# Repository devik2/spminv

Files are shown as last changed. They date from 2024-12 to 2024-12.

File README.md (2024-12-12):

# spminv

Simple IGBT motor inverter

Initial idea was independent but in 2024 when I started I borrowed
idea of heatsink from from STMBL project.

There are differences from STMBL, only one MCU located on power N potential,
1xCAN,2xRS422 RX and 2xRS485 RX/TX for encoder/communications and separated
by galvanical isolators.

Flyback power supply for 15V/3V3 on N side and 5V for isolated side. Thus only
input is 90-350V DC.
This is because my main usage is for spindle motors where driver is located near
spindle and not in remote cabinet.

Why not use STMBL ? I wanted to use different IPM, integrate it into CAN network
of my homemade CNC and to play with FOC by myself. 
And I already use my 60V BLDC driver for 3 years and started this "upgrade" before
I found STMBL.

[And have to say, I'd stay with 60V mosfet inverter but it is hard to find quality(!)
 motors. All low ripple hi-torque I found are 200V rated]

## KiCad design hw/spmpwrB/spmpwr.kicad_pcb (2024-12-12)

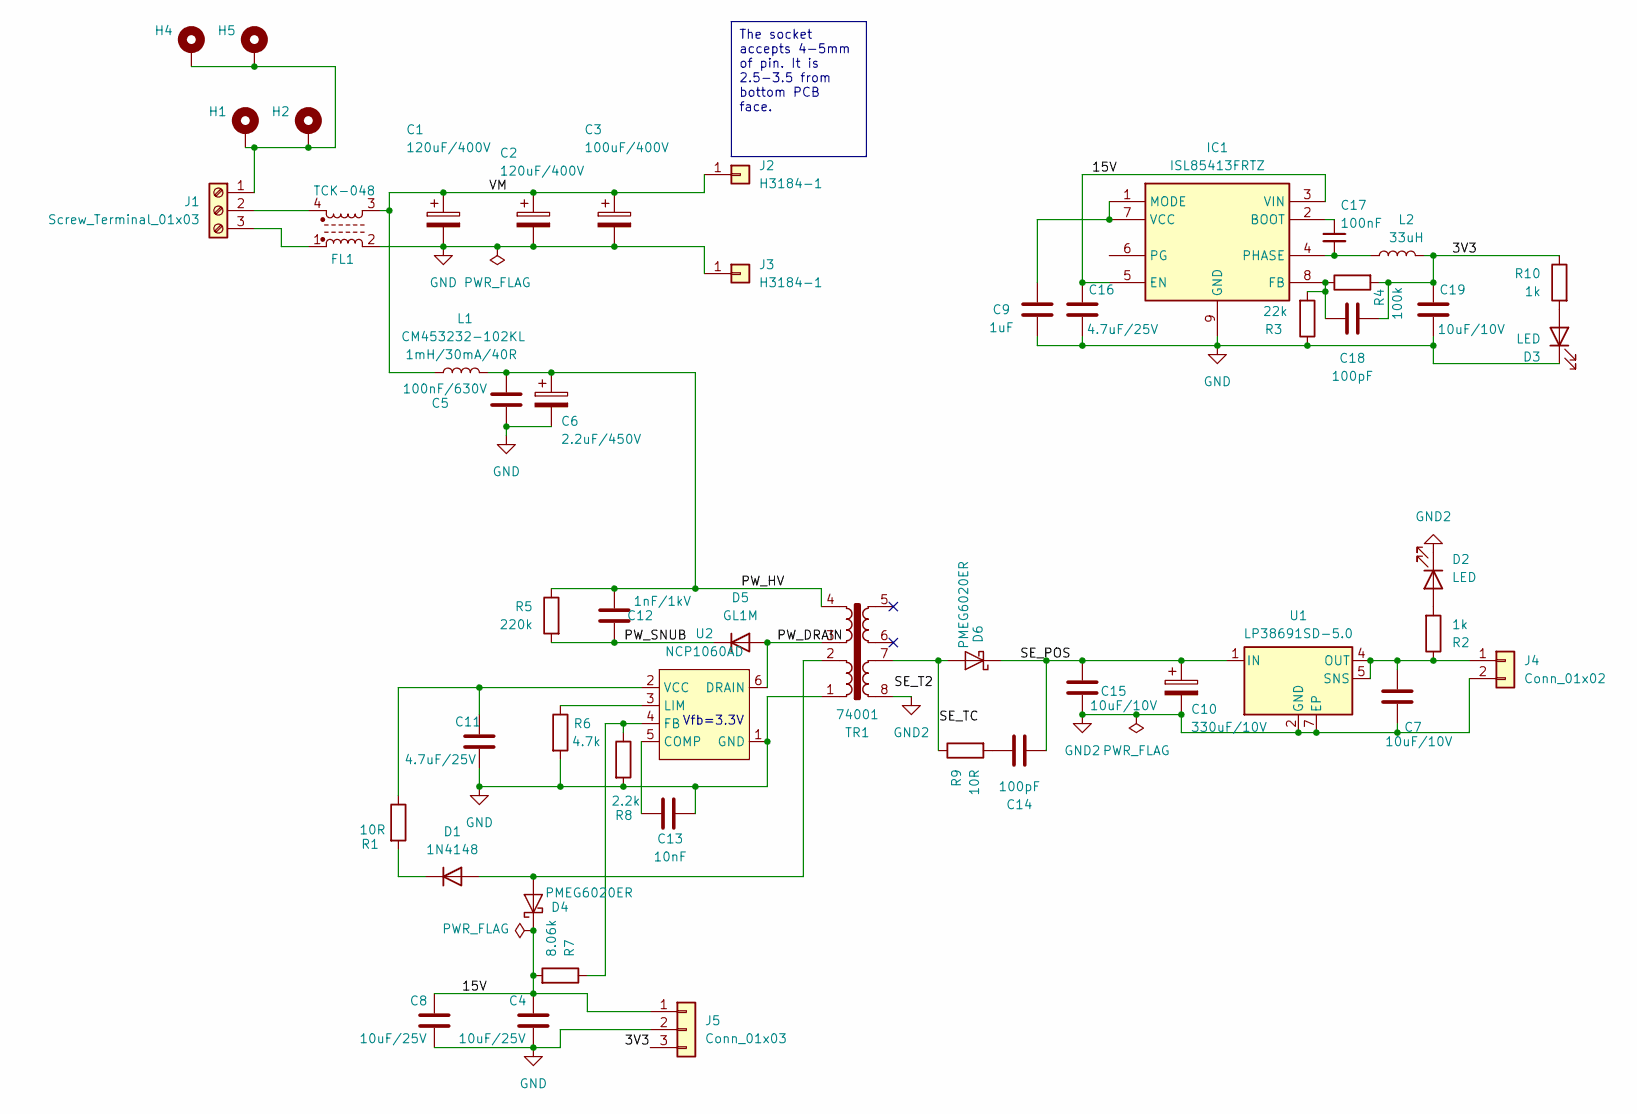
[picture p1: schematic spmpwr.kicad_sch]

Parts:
C1, C2: 120uF/400V; CP_Radial_D18.0mm_P7.50mm; Partno 400HXW120MEFR18X
C3: 100uF/400V; CP_Radial_D16.0mm_P7.50mm; Partno 400HXW100MEFR16X
C4, C8: 10uF/25V; C_1206_3216Metric
C5: 100nF/630V; C_1210_3225Metric
C6: 2.2uF/450V; CP_Radial_D6.3mm_P2.50mm
C7, C15, C19: 10uF/10V; C_0805_2012Metric_Pad1.18x1.45mm_HandSolder
C9: 1uF; C_0603_1608Metric_Pad1.08x0.95mm_HandSolder
C10: 330uF/10V; CP_Radial_D6.3mm_P2.50mm; Partno APSE6R3EC3561MF08S
C11, C16: 4.7uF/25V; C_0805_2012Metric_Pad1.18x1.45mm_HandSolder
C12: 1nF/1kV; C_1206_3216Metric_Pad1.33x1.80mm_HandSolder
C13: 10nF; C_0603_1608Metric_Pad1.08x0.95mm_HandSolder
C14, C18: 100pF; C_0603_1608Metric_Pad1.08x0.95mm_HandSolder
C17: 100nF; C_0603_1608Metric
D1: 1N4148; D_MiniMELF
D2, D3: LED; LED_0603_1608Metric
D4, D6: PMEG6020ER; D_SOD-123F
D5: GL1M; D_MiniMELF
FL1: L_Ferrite_Coupled_1243; Choke_common_12.0x12.0mm_P7.62; Partno TCK-048
H1, H2, H4, H5: MountingHole_Pad; MountingHole_3.2mm_M3_DIN965_Pad_TopBottom
IC1: ISL85413FRTZ; WSON-8-1EP_3x3mm_P0.5mm_EP1.2x2mm; Manufacturer_Part_Number ISL85413FRTZ
J1: Screw_Terminal_01x03; Altech_AK300_1x03_P5.00mm_45-Degree
J2, J3: H3184-1; H318401
J4: Conn_01x02; PinHeader_1x02_P2.54mm_Vertical
J5: Conn_01x03; PinHeader_1x03_P2.54mm_Vertical
L1: 1mH/30mA/40R; L_1812_4532Metric_Pad1.30x3.40mm_HandSolder; Partno CM453232-102KL
L2: 33uH; L_Abracon_ASPI-3012S; Partno 74404032330
R1, R9: 10R; R_0603_1608Metric_Pad0.98x0.95mm_HandSolder
R2, R10: 1k; R_0603_1608Metric_Pad0.98x0.95mm_HandSolder
R3: 22k; R_0603_1608Metric_Pad0.98x0.95mm_HandSolder
R4: 100k; R_0603_1608Metric_Pad0.98x0.95mm_HandSolder
R5: 220k; R_1206_3216Metric_Pad1.30x1.75mm_HandSolder
R6: 4.7k; R_0603_1608Metric_Pad0.98x0.95mm_HandSolder
R7: 8.06k; R_0603_1608Metric_Pad0.98x0.95mm_HandSolder
R8: 2.2k; R_0603_1608Metric_Pad0.98x0.95mm_HandSolder
TR1: 74001; Myrra_74000
U1: LP38691SD-5.0; WSON-6-1EP_3x3mm_P0.95mm
U2: NCP1060AD; SSOP-10_3.9x4.9mm_P1.00mm

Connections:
/3V3: C18.1, C19.1, J5.3, L2.2, R4.2, R10.1
/15V: C4.1, C8.1, C16.1, D4.1 (K), IC1.3 (VIN), IC1.5 (EN), J5.1, R7.2
/PW_DRAIN: D5.2 (A), TR1.3, U2.6 (DRAIN), U2.7 (DRAIN), U2.8 (DRAIN), U2.9 (DRAIN), U2.10 (DRAIN)
/PW_HV: C5.1, C6.1, C12.1, L1.2, R5.1, TR1.4
/PW_SNUB: C12.2, D5.1 (K), R5.2
/SE_POS: C10.1, C14.2, C15.1, D6.1 (K), U1.1 (IN), U1.6 (IN)
/SE_TC: D6.2 (A), R9.1, TR1.7
/VM: C1.1, C2.1, C3.1, FL1.3, J2.1, L1.1
GND: C1.2, C2.2, C3.2, C4.2, C5.2, C6.2, C8.2, C9.2, C11.2, C13.2, C16.2, C19.2, D3.1 (K), FL1.2, IC1.9 (GND), J3.1, J5.2, R3.1, R6.2, R8.2, TR1.1, U2.1 (GND)
GND2: C7.2, C10.2, C15.2, D2.1 (K), J4.2, TR1.8, U1.2 (GND), U1.7 (EP)
unnamed: C14.1, R9.2
unnamed: D1.2 (A), D4.2 (A), TR1.2
unnamed: D1.1 (K), R1.2
unnamed: D2.2 (A), R2.2
unnamed: D3.2 (A), R10.2
unnamed: C17.1, IC1.2 (BOOT)
unnamed: C18.2, IC1.8 (FB), R3.2, R4.1
unnamed: C9.1, IC1.1 (MODE), IC1.7 (VCC)
unnamed: C17.2, IC1.4 (PHASE), L2.1
unnamed: H1.1, H2.1, H4.1, H5.1, J1.1
unnamed: FL1.4, J1.2
unnamed: FL1.1, J1.3
unnamed: C7.1, J4.1, R2.1, U1.4 (OUT), U1.5 (SNS)
unnamed: C13.1, U2.5 (COMP)
unnamed: R7.1, R8.1, U2.4 (FB)
unnamed: R6.1, U2.3 (LIM)
unnamed: C11.1, R1.1, U2.2 (VCC)

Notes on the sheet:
The socket accepts 4-5mm of pin. It is 2.5-3.5 from bottom PCB face.
Vfb=3.3V

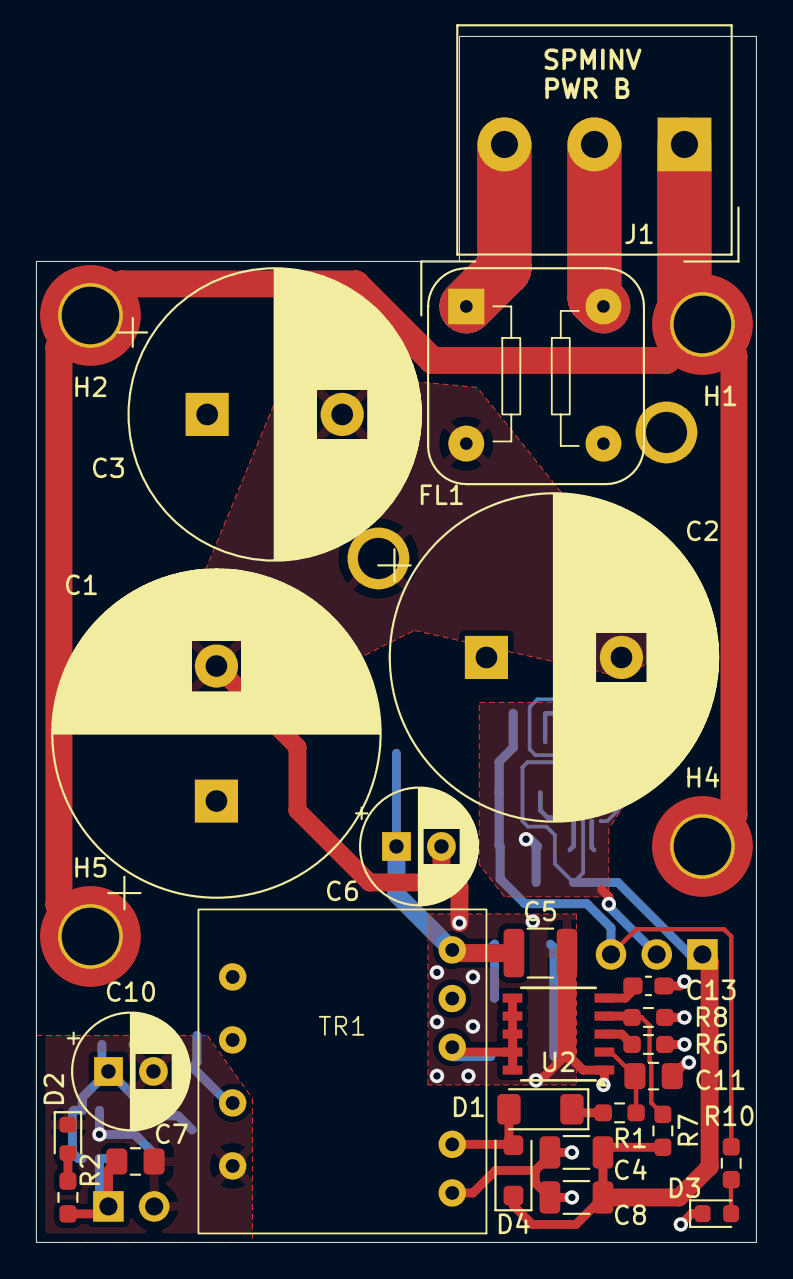
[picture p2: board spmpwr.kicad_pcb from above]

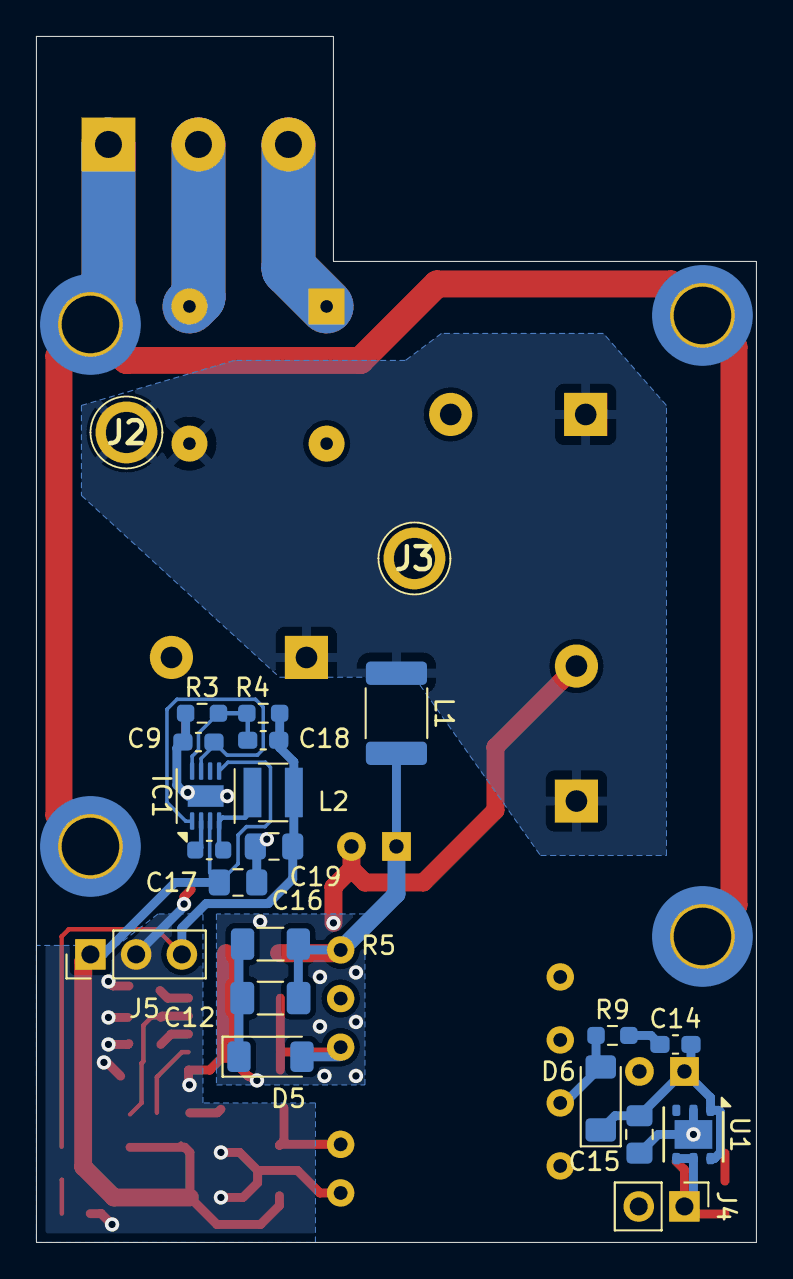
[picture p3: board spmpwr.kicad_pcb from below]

Board: 2 copper layers, 40.0 x 67.0 mm, 51 parts (22 on the bottom side), 27 nets.

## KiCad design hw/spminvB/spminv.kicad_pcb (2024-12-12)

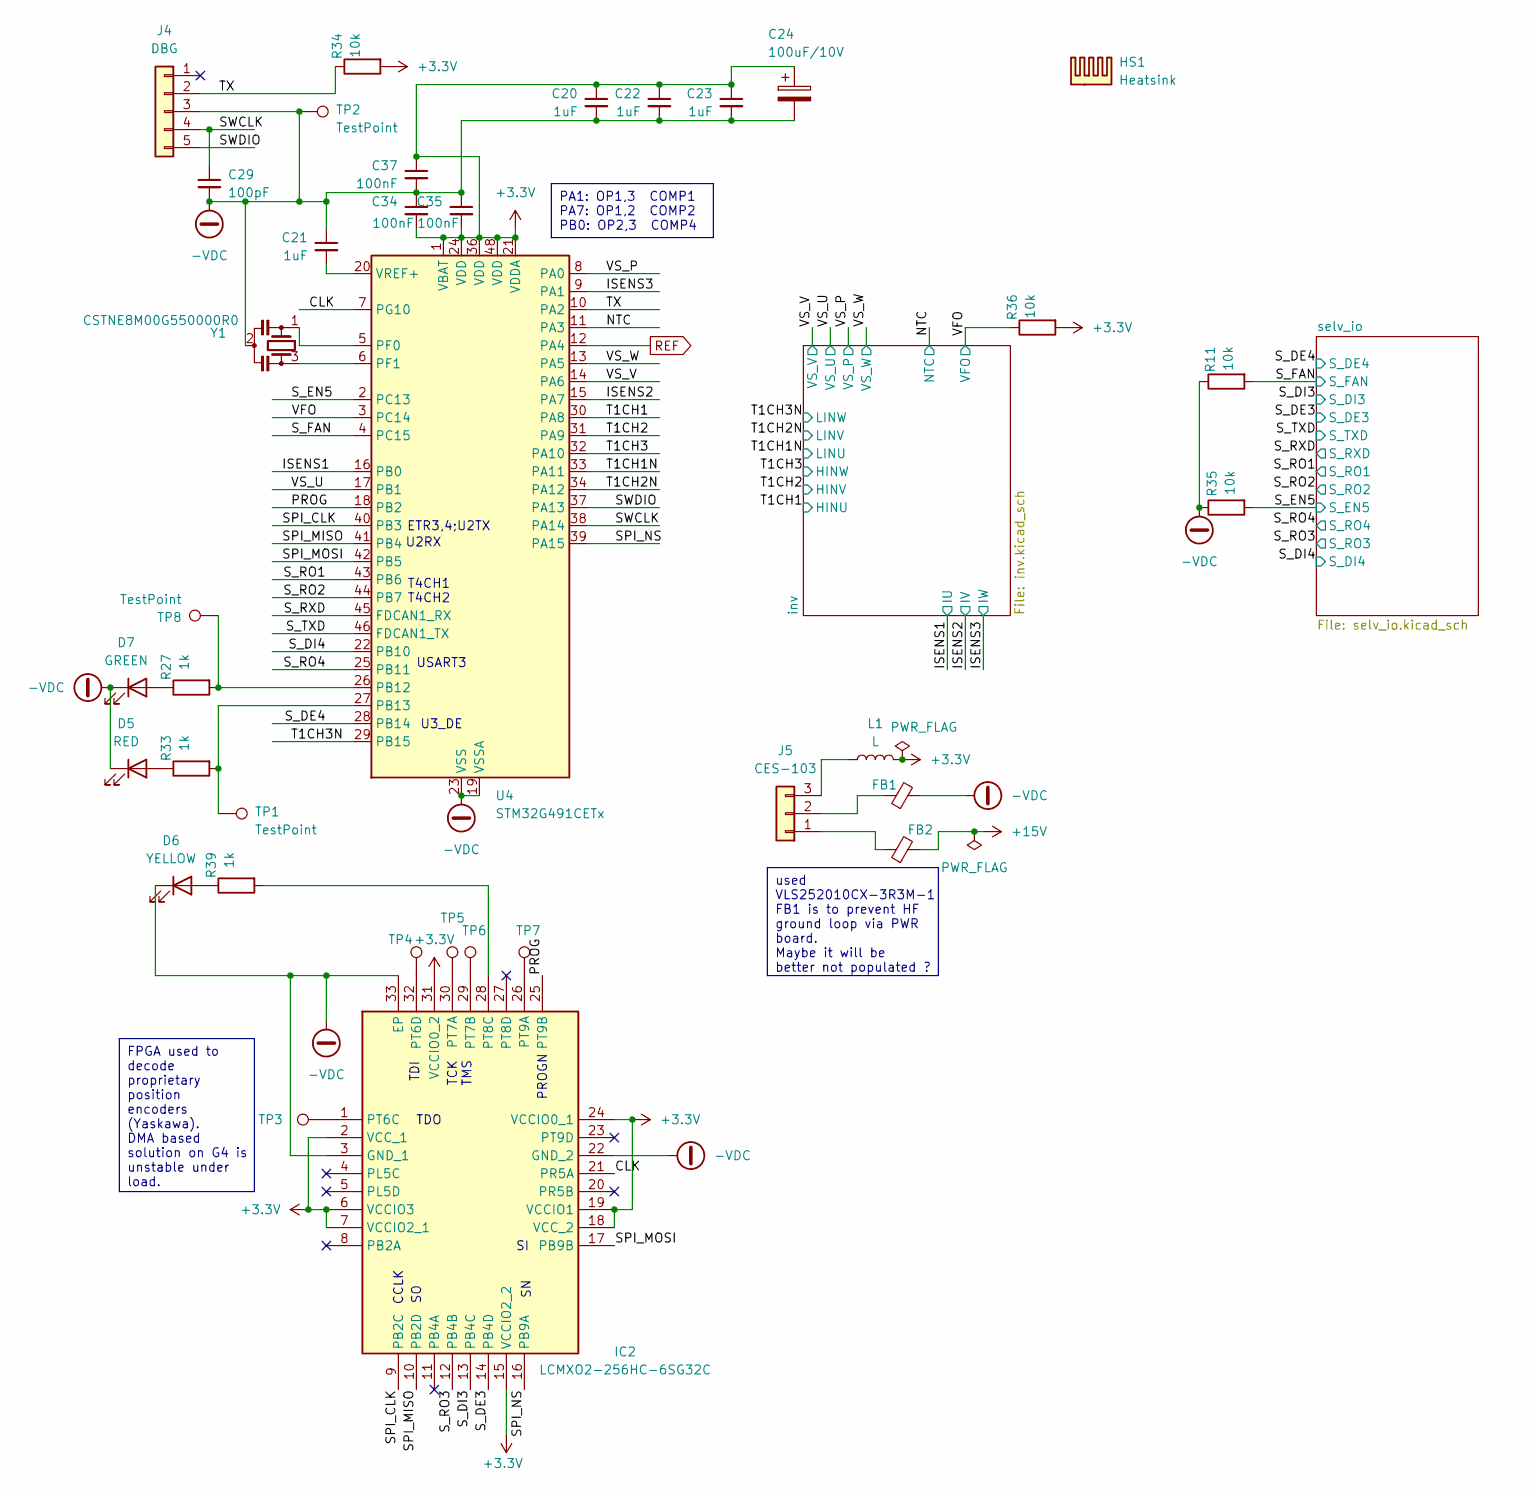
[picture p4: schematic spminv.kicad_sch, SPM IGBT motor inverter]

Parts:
C20, C21, C22, C23: 1uF; C_0603_1608Metric_Pad1.08x0.95mm_HandSolder
C24: 100uF/10V; CP_EIA-6032-28_Kemet-C
C29: 100pF; C_0603_1608Metric_Pad1.08x0.95mm_HandSolder
C34, C35, C37: 100nF; C_0603_1608Metric_Pad1.08x0.95mm_HandSolder
D5: RED; LED_0603_1608Metric
D6: YELLOW; LED_0603_1608Metric
D7: GREEN; LED_0603_1608Metric
FB1, FB2: FerriteBead_Small; L_1206_3216Metric
HS1: Heatsink; Heatsink_Stonecold_HS-S03_13.21x12.7mm
IC2: LCMXO2-256HC-6SG32C; QFN-32-1EP_5x5mm_P0.5mm_EP3.3x3.3mm; Manufacturer_Part_Number LCMXO2-256HC-6SG32C; Mouser Part Number 842-MXO2-256HC6SG32C
J4: DBG; Molex_PicoBlade_53048-0510_1x05_P1.25mm_Horizontal
J5: CES-103; PinSocket_1x03_P2.54mm_Vertical
L1: L; L_1206_3216Metric
R11, R34, R35, R36: 10k; R_0603_1608Metric_Pad0.98x0.95mm_HandSolder
R27, R33, R39: 1k; R_0603_1608Metric_Pad0.98x0.95mm_HandSolder
TP1, TP2, TP3, TP4, TP5, TP6, TP7, TP8: TestPoint; TestPoint_THTPad_D1.0mm_Drill0.5mm
U4: STM32G491CETx; LQFP-48_7x7mm_P0.5mm
Y1: CSTNE8M00G550000R0; Resonator_SMD_Murata_CSTxExxV-3Pin_3.0x1.1mm

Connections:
+3.3V: C20.1, C22.1, C23.1, C24.1, C34.2, C35.2, C37.1, IC2.2 (VCC_1), IC2.6 (VCCIO3), IC2.7 (VCCIO2_1), IC2.15 (VCCIO2_2), IC2.18 (VCC_2), IC2.19 (VCCIO1), IC2.24 (VCCIO0_1), IC2.31 (VCCIO0_2), L1.2, R34.2, R36.2, U4.1 (VBAT), U4.21 (VDDA), U4.24 (VDD), U4.36 (VDD), U4.48 (VDD); also elsewhere on the board
+15V: FB2.2; also elsewhere on the board
-VDC: C20.2, C21.1, C22.2, C23.2, C24.2, C29.2, C34.1, C35.1, C37.2, D5.1 (K), D6.1 (K), D7.1 (K), FB1.2, IC2.3 (GND_1), IC2.22 (GND_2), IC2.33 (EP), J4.3, R11.1, R35.1, TP2.1, U4.19 (VSSA), U4.23 (VSS), U4.35 (VSS), U4.47 (VSS), Y1.2; also elsewhere on the board
/CLK: IC2.21 (PR5A), U4.7 (PG10)
/ISENS1: U4.16 (PB0); also elsewhere on the board
/ISENS2: U4.15 (PA7); also elsewhere on the board
/ISENS3: U4.9 (PA1); also elsewhere on the board
/NTC: U4.11 (PA3); also elsewhere on the board
/PROG: IC2.25 (PT9B), U4.18 (PB2)
/SPI_CLK: IC2.9 (PB2C), U4.40 (PB3)
/SPI_MISO: IC2.10 (PB2D), U4.41 (PB4)
/SPI_MOSI: IC2.17 (PB9B), U4.42 (PB5)
/SPI_NS: IC2.16 (PB9A), U4.39 (PA15)
/SWCLK: C29.1, J4.4, U4.38 (PA14)
/SWDIO: J4.5, U4.37 (PA13)
/S_DE3: IC2.14 (PB4D); also elsewhere on the board
/S_DE4: U4.28 (PB14); also elsewhere on the board
/S_DI3: IC2.13 (PB4C); also elsewhere on the board
/S_DI4: U4.22 (PB10); also elsewhere on the board
/S_EN5: R35.2, U4.2 (PC13); also elsewhere on the board
/S_FAN: R11.2, U4.4 (PC15); also elsewhere on the board
/S_RO1: U4.43 (PB6); also elsewhere on the board
/S_RO2: U4.44 (PB7); also elsewhere on the board
/S_RO3: IC2.12 (PB4B); also elsewhere on the board
/S_RO4: U4.25 (PB11); also elsewhere on the board
/S_RXD: U4.45 (FDCAN1_RX); also elsewhere on the board
/S_TXD: U4.46 (FDCAN1_TX); also elsewhere on the board
/T1CH1: U4.30 (PA8); also elsewhere on the board
/T1CH1N: U4.33 (PA11); also elsewhere on the board
/T1CH2: U4.31 (PA9); also elsewhere on the board
/T1CH2N: U4.34 (PA12); also elsewhere on the board
/T1CH3: U4.32 (PA10); also elsewhere on the board
/T1CH3N: U4.29 (PB15); also elsewhere on the board
/TX: J4.2, R34.1, U4.10 (PA2)
/VFO: R36.1, U4.3 (PC14); also elsewhere on the board
/VS_P: U4.8 (PA0); also elsewhere on the board
/VS_U: U4.17 (PB1); also elsewhere on the board
/VS_V: U4.14 (PA6); also elsewhere on the board
/VS_W: U4.13 (PA5); also elsewhere on the board
unnamed: D5.2 (A), R33.1
unnamed: D6.2 (A), R39.1
unnamed: D7.2 (A), R27.1
unnamed: IC2.1 (PT6C), TP3.1
unnamed: IC2.32 (PT6D), TP4.1
unnamed: IC2.30 (PT7A), TP5.1
unnamed: IC2.29 (PT7B), TP6.1
unnamed: IC2.28 (PT8C), R39.2
unnamed: IC2.26 (PT9A), TP7.1
unnamed: FB2.1, J5.1
unnamed: FB1.1, J5.2
unnamed: J5.3, L1.1
unnamed: R27.2, TP8.1, U4.26 (PB12)
unnamed: R33.2, TP1.1, U4.27 (PB13)
unnamed: U4.5 (PF0), Y1.1
unnamed: U4.6 (PF1), Y1.3
unnamed: C21.2, U4.20 (VREF+)
REF: U4.12 (PA4); also elsewhere on the board

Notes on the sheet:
PA1: OP1,3 COMP1 PA7: OP1,2 COMP2 PB0: OP2,3 COMP4
FPGA used to decode proprietary position encoders (Yaskawa). DMA based solution on G4 is unstable under load.
used VLS252010CX-3R3M-1 FB1 is to prevent HF ground loop via PWR board. Maybe it will be better not populated ?
TDI
PROGN
TDO
USART3
T4CH1 T4CH2
TCK TMS
U2RX
ETR3,4;U2TX
U3_DE
CCLK

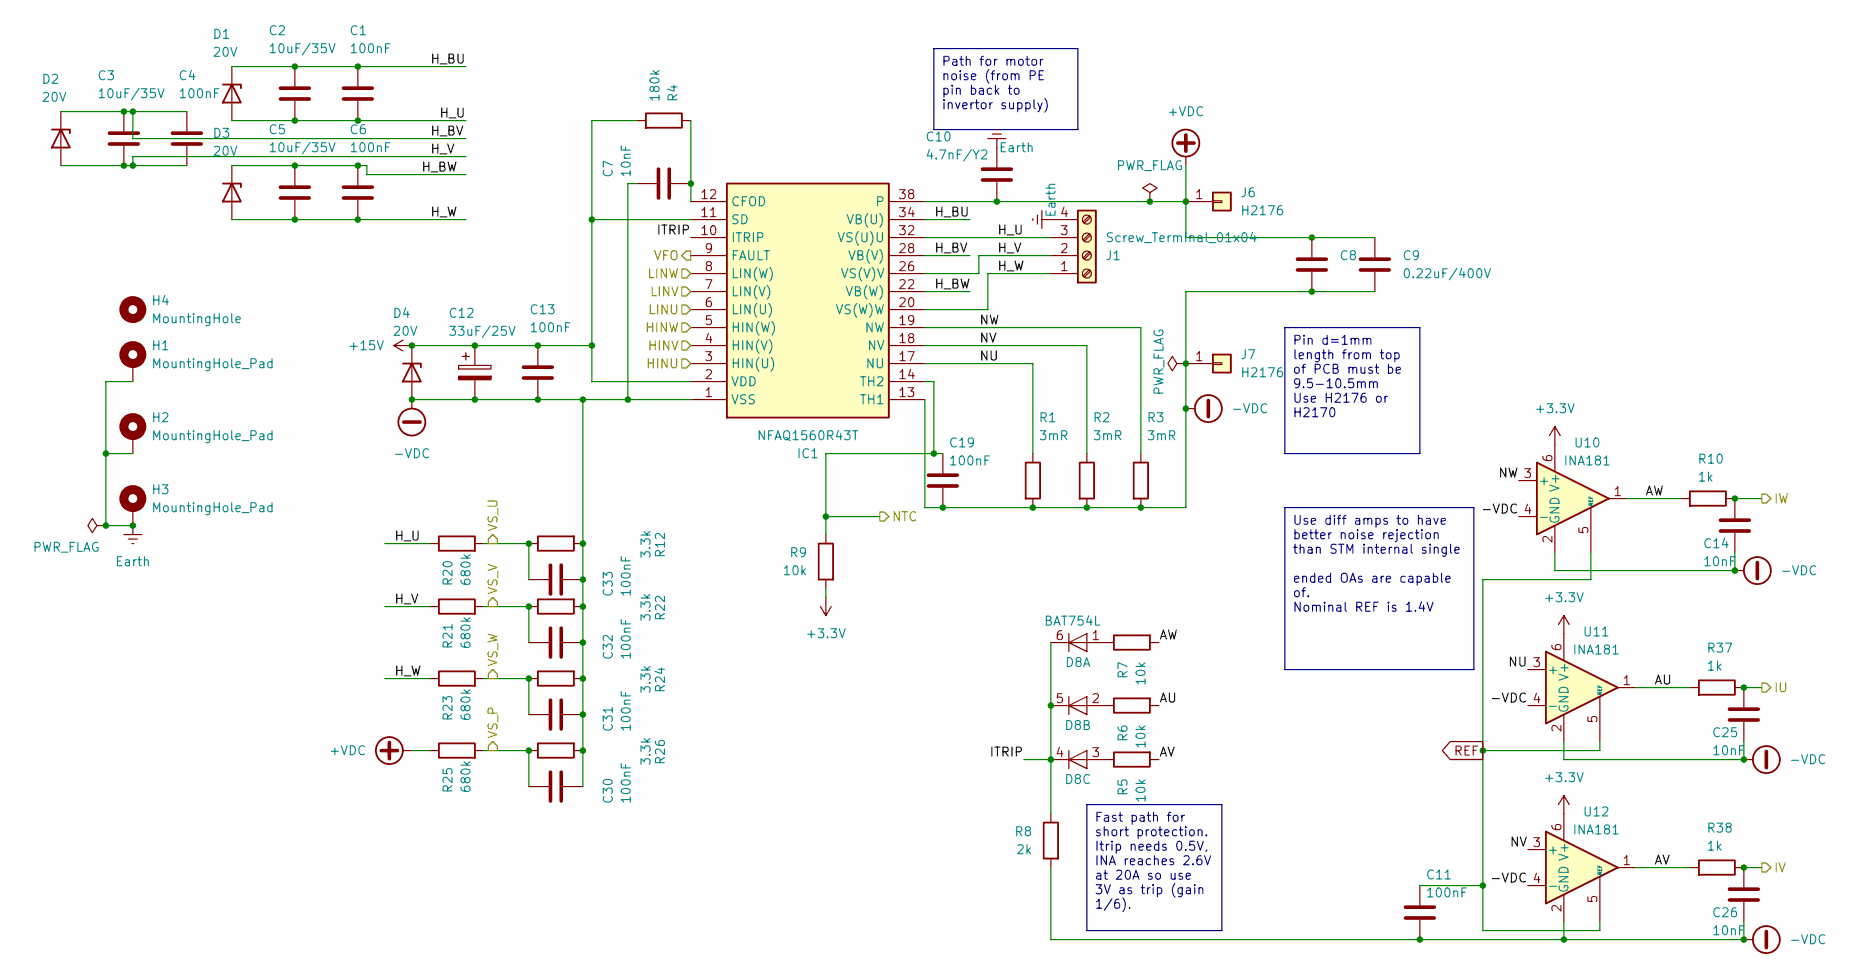
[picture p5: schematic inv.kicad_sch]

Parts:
C1, C4, C6, C11, C13, C19, C30, C31, C32, C33: 100nF; C_0603_1608Metric
C2, C3, C5: 10uF/35V; C_1210_3225Metric
C7, C14, C25, C26: 10nF; C_0603_1608Metric
C8, C9: 0.22uF/400V; C_2220_5750Metric_Pad1.97x5.40mm_HandSolder
C10: 4.7nF/Y2; C_2220_5750Metric
C12: 33uF/25V; CP_EIA-6032-28_Kemet-C
D1, D2, D3, D4: 20V; D_MiniMELF; Partno BZV55C20
D8: BAT754L; SOT-363_SC-70-6
H1, H2, H3: MountingHole_Pad; MountingHole_3.2mm_M3_DIN965_Pad_TopBottom
H4: MountingHole; MountingHole_3.2mm_M3_DIN965
IC1: NFAQ1560R43T; Manufacturer_Part_Number NFAQ1560R43T; Mouser Part Number 863-NFAQ1560R43T
J1: Screw_Terminal_01x04; Altech_AK300_1x04_P5.00mm_45-Degree
J6, J7: H2176; Pin_D1.3mm_L11.0mm
R1, R2, R3: 3mR; R_1206_3216Metric
R4: 180k; R_0603_1608Metric_Pad0.98x0.95mm_HandSolder
R5, R6, R7, R9: 10k; R_0603_1608Metric_Pad0.98x0.95mm_HandSolder
R8: 2k; R_0603_1608Metric_Pad0.98x0.95mm_HandSolder
R10, R37, R38: 1k; R_0603_1608Metric_Pad0.98x0.95mm_HandSolder
R12, R22, R24, R26: 3.3k; R_0603_1608Metric_Pad0.98x0.95mm_HandSolder
R20, R21, R23, R25: 680k; R_MiniMELF_MMA-0204
U10, U11, U12: INA181; SOT-363_SC-70-6

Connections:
+3.3V: R9.2, U10.6 (V+), U11.6 (V+), U12.6 (V+); also elsewhere on the board
+15V: C12.1, C13.1, D4.1 (K), IC1.2 (VDD), IC1.11 (SD), R4.2; also elsewhere on the board
+VDC: C8.1, C9.1, C10.2, IC1.38, J6.1, R25.1
-VDC: C7.1, C8.2, C9.2, C11.2, C12.2, C13.2, C14.2, C19.2, C25.2, C26.2, C30.2, C31.2, C32.2, C33.2, D4.2 (A), IC1.1 (VSS), IC1.13 (TH1), J7.1, R1.2, R2.2, R3.2, R8.2, R12.2, R22.2, R24.2, R26.2, U10.2 (GND), U10.4 (-), U11.2 (GND), U11.4 (-), U12.2 (GND), U12.4 (-); also elsewhere on the board
/ISENS1: C25.1, R37.1; also elsewhere on the board
/ISENS2: C26.1, R38.1; also elsewhere on the board
/ISENS3: C14.1, R10.1; also elsewhere on the board
/NTC: C19.1, IC1.14 (TH2), R9.1; also elsewhere on the board
/T1CH1: IC1.3 (HIN(U)); also elsewhere on the board
/T1CH1N: IC1.6 (LIN(U)); also elsewhere on the board
/T1CH2: IC1.4 (HIN(V)); also elsewhere on the board
/T1CH2N: IC1.7 (LIN(V)); also elsewhere on the board
/T1CH3: IC1.5 (HIN(W)); also elsewhere on the board
/T1CH3N: IC1.8 (LIN(W)); also elsewhere on the board
/VFO: IC1.9 (FAULT); also elsewhere on the board
/VS_P: C30.1, R25.2, R26.1; also elsewhere on the board
/VS_U: C33.1, R12.1, R20.2; also elsewhere on the board
/VS_V: C32.1, R21.2, R22.1; also elsewhere on the board
/VS_W: C31.1, R23.2, R24.1; also elsewhere on the board
/inv/AU: R6.2, R37.2, U11.1
/inv/AV: R5.2, R38.2, U12.1
/inv/AW: R7.2, R10.2, U10.1
/inv/H_BU: C1.1, C2.1, D1.1 (K), IC1.34 (VB(U))
/inv/H_BV: C3.1, C4.1, D2.1 (K), IC1.28 (VB(V))
/inv/H_BW: C5.1, C6.1, D3.1 (K), IC1.22 (VB(W))
/inv/H_U: C1.2, C2.2, D1.2 (A), IC1.32 (VS(U)U), J1.3, R20.1
/inv/H_V: C3.2, C4.2, D2.2 (A), IC1.26 (VS(V)V), J1.2, R21.1
/inv/H_W: C5.2, C6.2, D3.2 (A), IC1.20 (VS(W)W), J1.1, R23.1
/inv/ITRIP: D8.4 (K), D8.5 (K), D8.6 (K), IC1.10 (ITRIP), R8.1
/inv/NU: IC1.17 (NU), R1.1, U11.3 (+)
/inv/NV: IC1.18 (NV), R2.1, U12.3 (+)
/inv/NW: IC1.19 (NW), R3.1, U10.3 (+)
Earth: C10.1, H1.1, H2.1, H3.1, J1.4
unnamed: D8.1 (A), R7.1
unnamed: D8.2 (A), R6.1
unnamed: D8.3 (A), R5.1
unnamed: C7.2, IC1.12 (CFOD), R4.1
REF: C11.1, U10.5 (REF), U11.5 (REF), U12.5 (REF); also elsewhere on the board

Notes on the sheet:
Pin d=1mm length from top of PCB must be 9.5-10.5mm Use H2176 or H2170
Fast path for short protection. Itrip needs 0.5V, INA reaches 2.6V at 20A so use 3V as trip (gain 1/6).
Use diff amps to have better noise rejection than STM internal single ended OAs are capable of. Nominal REF is 1.4V
Path for motor noise (from PE pin back to invertor supply)

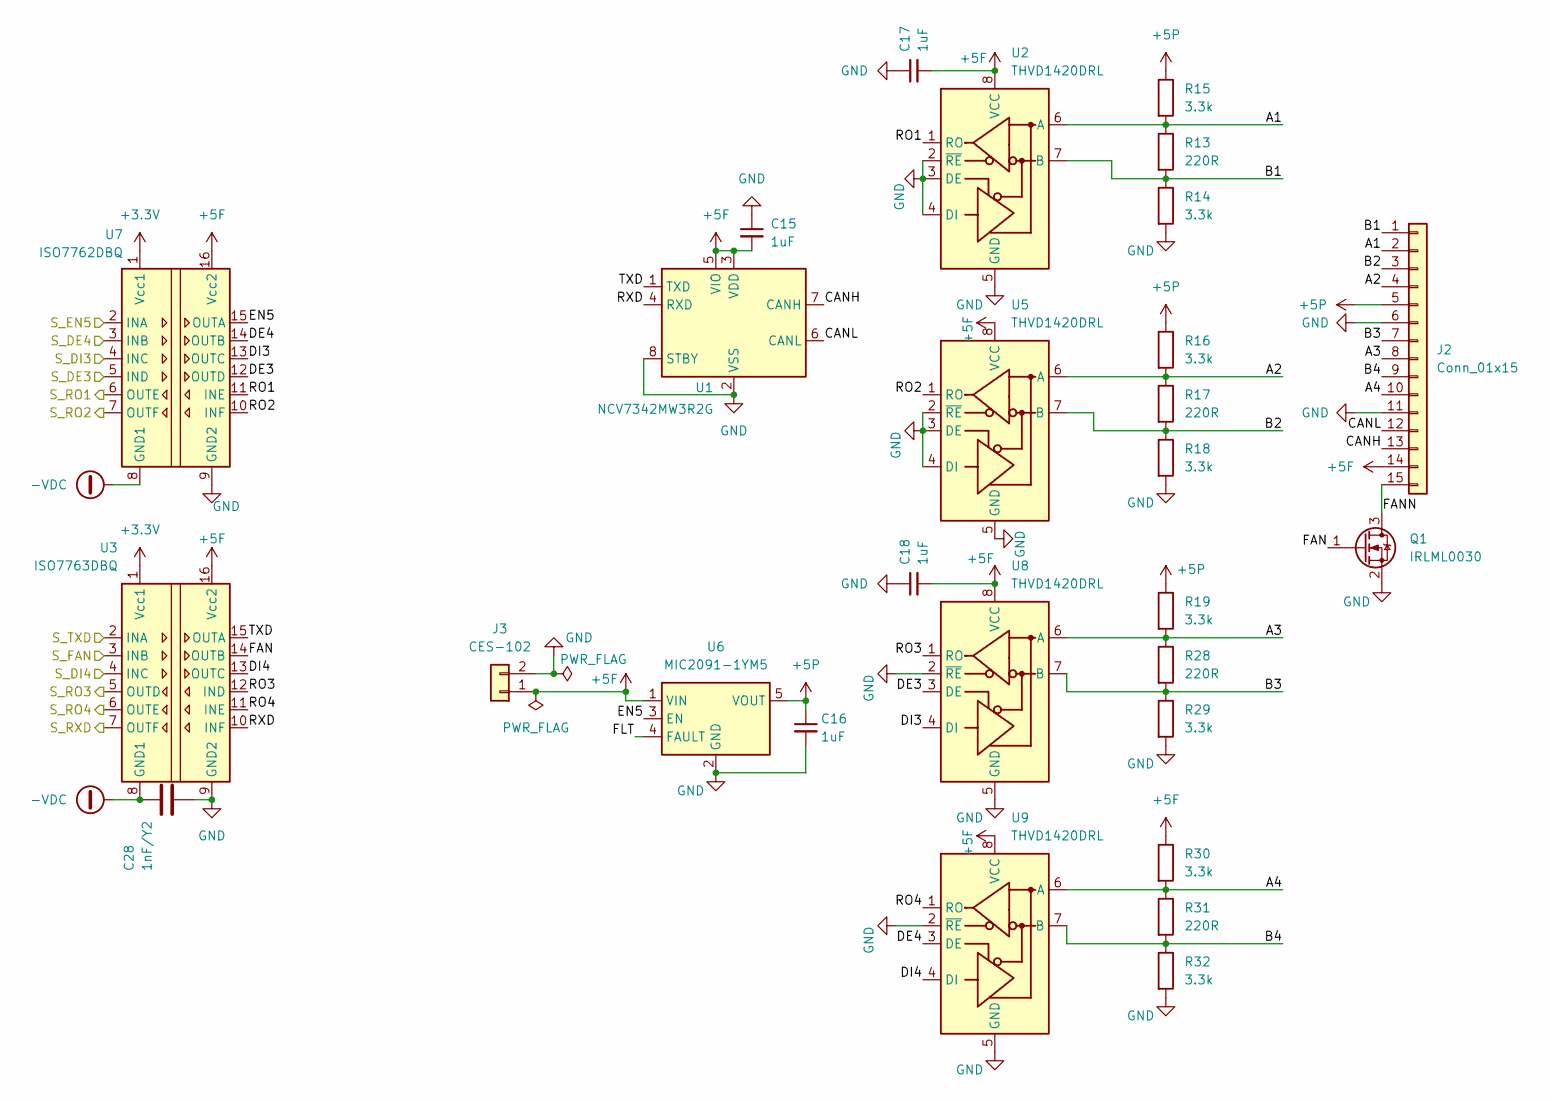
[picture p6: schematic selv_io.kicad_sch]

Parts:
C15, C16, C17, C18: 1uF; C_0603_1608Metric_Pad1.08x0.95mm_HandSolder
C28: 1nF/Y2; C_2220_5750Metric
J2: Conn_01x15; CUI_TBL009V-254-15BE-2BE
J3: CES-102; PinSocket_1x02_P2.54mm_Vertical
Q1: IRLML0030; SOT-23
R13, R17, R28, R31: 220R; R_0805_2012Metric
R14, R15, R16, R18, R19, R29, R30, R32: 3.3k; R_0805_2012Metric
U1: NCV7342MW3R2G; DFN-8-1EP_3x3mm_P0.65mm_EP1.55x2.4mm
U2, U5, U8, U9: THVD1420DRL; Texas_VSON-HR-8_1.5x2mm_P0.5mm
U3: ISO7763DBQ; SSOP-16_3.9x4.9mm_P0.635mm
U6: MIC2091-1YM5; SOT-23-5
U7: ISO7762DBQ; SSOP-16_3.9x4.9mm_P0.635mm

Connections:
+3.3V: U3.1 (Vcc1), U7.1 (Vcc1); also elsewhere on the board
+5F: C15.2, C17.2, C18.2, J2.14, J3.1, R30.1, U1.3 (VDD), U1.5 (VIO), U2.8 (VCC), U3.16 (Vcc2), U5.8 (VCC), U6.1 (VIN), U7.16 (Vcc2), U8.8 (VCC), U9.8 (VCC)
+5P: C16.1, J2.5, R15.1, R16.1, R19.1, U6.5 (VOUT)
-VDC: C28.1, U3.8 (GND1), U7.8 (GND1); also elsewhere on the board
/S_DE3: U7.5 (IND); also elsewhere on the board
/S_DE4: U7.3 (INB); also elsewhere on the board
/S_DI3: U7.4 (INC); also elsewhere on the board
/S_DI4: U3.4 (INC); also elsewhere on the board
/S_EN5: U7.2 (INA); also elsewhere on the board
/S_FAN: U3.3 (INB); also elsewhere on the board
/S_RO1: U7.6 (OUTE); also elsewhere on the board
/S_RO2: U7.7 (OUTF); also elsewhere on the board
/S_RO3: U3.5 (OUTD); also elsewhere on the board
/S_RO4: U3.6 (OUTE); also elsewhere on the board
/S_RXD: U3.7 (OUTF); also elsewhere on the board
/S_TXD: U3.2 (INA); also elsewhere on the board
/selv_io/A1: J2.2, R13.1, R15.2, U2.6 (A)
/selv_io/A2: J2.4, R16.2, R17.1, U5.6 (A)
/selv_io/A3: J2.8, R19.2, R28.1, U8.6 (A)
/selv_io/A4: J2.10, R30.2, R31.1, U9.6 (A)
/selv_io/B1: J2.1, R13.2, R14.1, U2.7 (B)
/selv_io/B2: J2.3, R17.2, R18.1, U5.7 (B)
/selv_io/B3: J2.7, R28.2, R29.1, U8.7 (B)
/selv_io/B4: J2.9, R31.2, R32.1, U9.7 (B)
/selv_io/CANH: J2.13, U1.7 (CANH)
/selv_io/CANL: J2.12, U1.6 (CANL)
/selv_io/DE3: U7.12 (OUTD), U8.3 (DE)
/selv_io/DE4: U7.14 (OUTB), U9.3 (DE)
/selv_io/DI3: U7.13 (OUTC), U8.4 (DI)
/selv_io/DI4: U3.13 (OUTC), U9.4 (DI)
/selv_io/EN5: U6.3 (EN), U7.15 (OUTA)
/selv_io/FAN: Q1.1 (G), U3.14 (OUTB)
/selv_io/FANN: J2.15, Q1.3 (D)
/selv_io/FLT: U6.4 (FAULT)
/selv_io/RO1: U2.1 (RO), U7.11 (INE)
/selv_io/RO2: U5.1 (RO), U7.10 (INF)
/selv_io/RO3: U3.12 (IND), U8.1 (RO)
/selv_io/RO4: U3.11 (INE), U9.1 (RO)
/selv_io/RXD: U1.4 (RXD), U3.10 (INF)
/selv_io/TXD: U1.1 (TXD), U3.15 (OUTA)
GND: C15.1, C16.2, C17.1, C18.1, C28.2, J2.6, J2.11, J3.2, Q1.2 (S), R14.2, R18.2, R29.2, R32.2, U1.2 (VSS), U1.8 (STBY), U1.9 (VSS), U2.2 (~RE), U2.3 (DE), U2.4 (DI), U2.5 (GND), U3.9 (GND2), U5.2 (~RE), U5.3 (DE), U5.4 (DI), U5.5 (GND), U6.2 (GND), U7.9 (GND2), U8.2 (~RE), U8.5 (GND), U9.2 (~RE), U9.5 (GND)

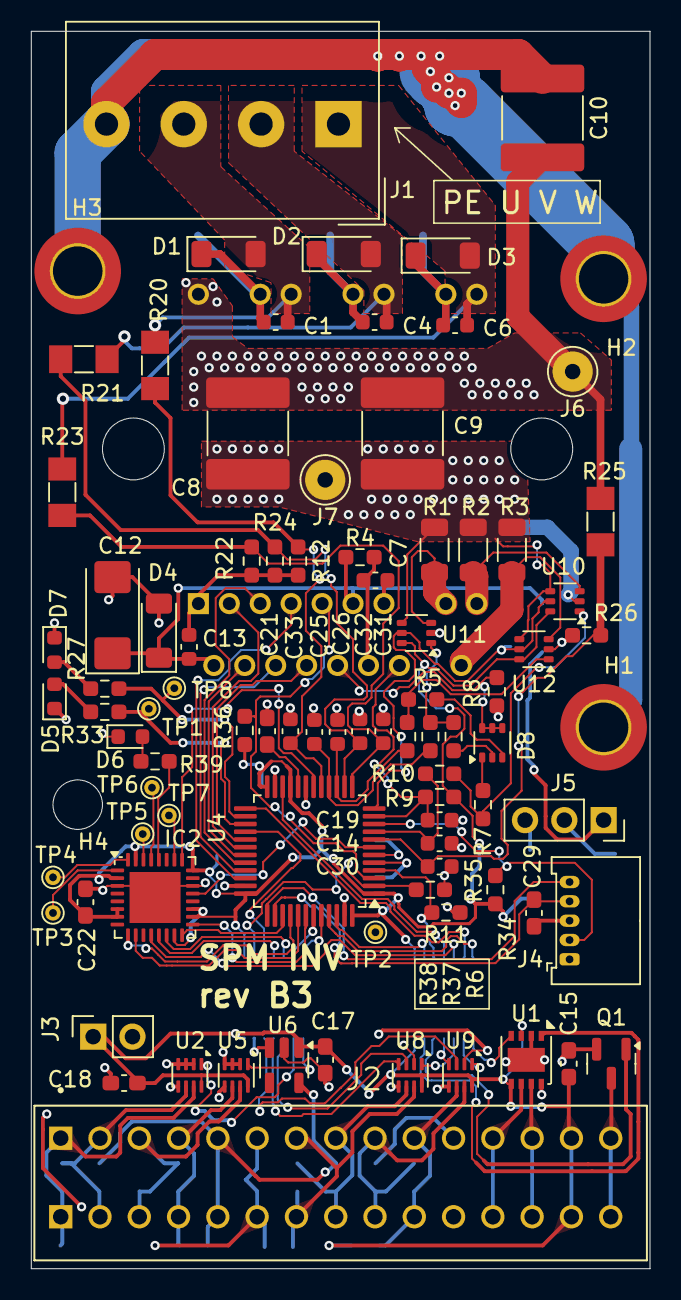
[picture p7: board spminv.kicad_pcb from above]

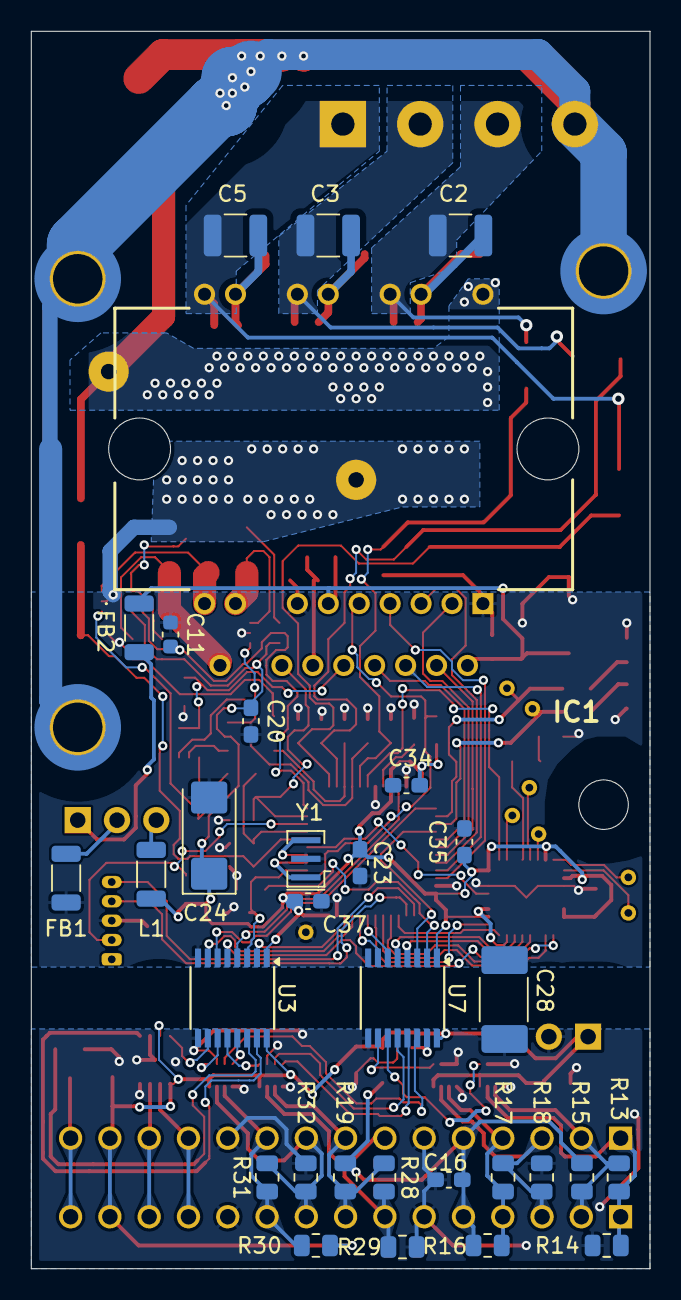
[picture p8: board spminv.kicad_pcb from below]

Board: 2 copper layers, 40.0 x 80.0 mm, 120 parts (31 on the bottom side), 102 nets.
